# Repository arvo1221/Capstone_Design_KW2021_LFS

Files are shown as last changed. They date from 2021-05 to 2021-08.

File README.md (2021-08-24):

# Capstone_Design_KW2021\
...

Environment : 

OS :16.04 ubuntu ros-kinetic \
Library  : PCL (at least 1.7) \
         : Eigen 3 \
         : RBDL 

# HardWare description



# System Architecture
캡스톤system아키텍처

#Video
https://www.youtube.com/watch?v=N5EMGGjnUHE

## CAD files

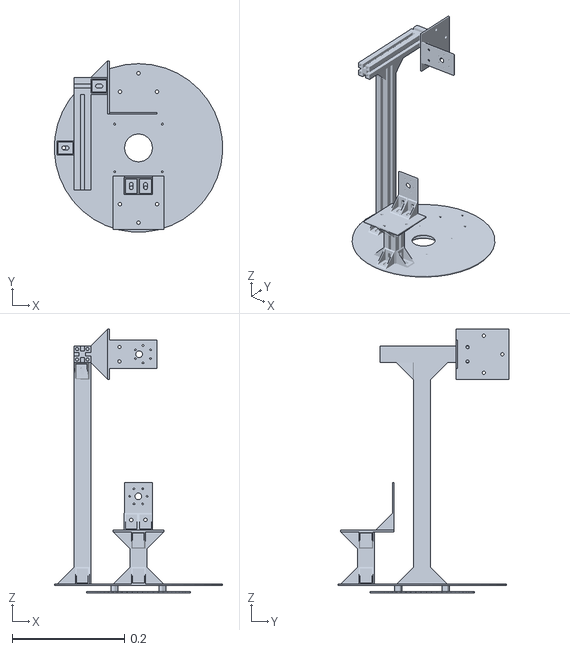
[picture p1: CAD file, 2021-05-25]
capstone_ws/src/turret_description/meshes/Yaw_link.STL
0.3 x 0.305 x 0.47

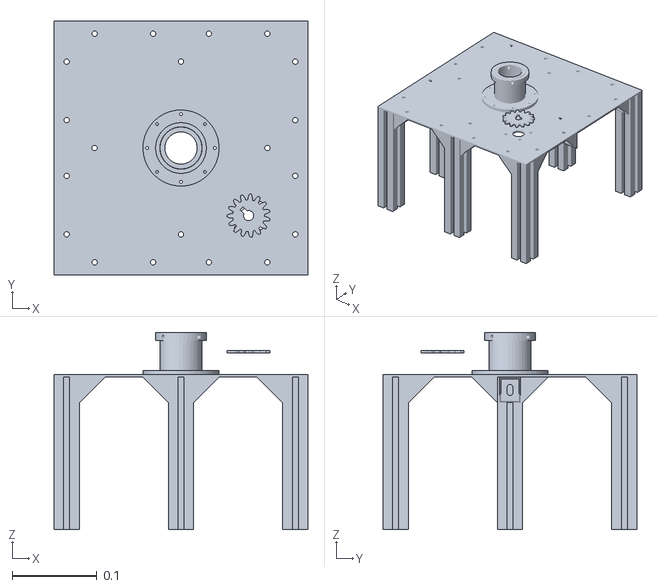
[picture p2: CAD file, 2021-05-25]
capstone_ws/src/turret_description/meshes/Base_link.STL
0.3 x 0.3 x 0.233

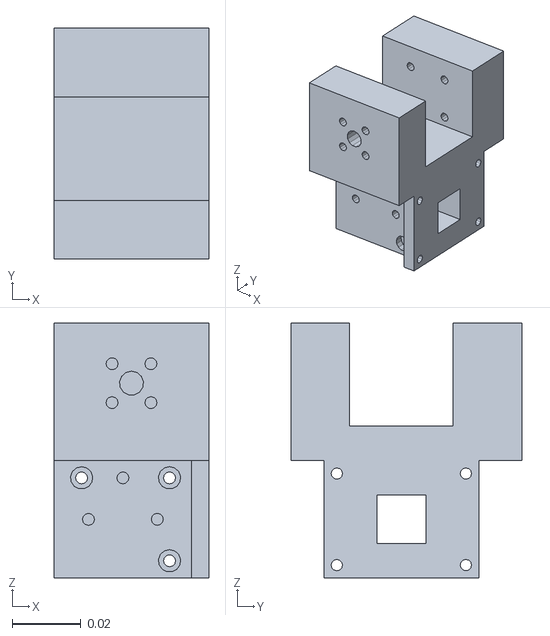
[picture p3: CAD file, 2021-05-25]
capstone_ws/src/turret_description/meshes/Pitch_link.STL
0.045 x 0.067 x 0.0741

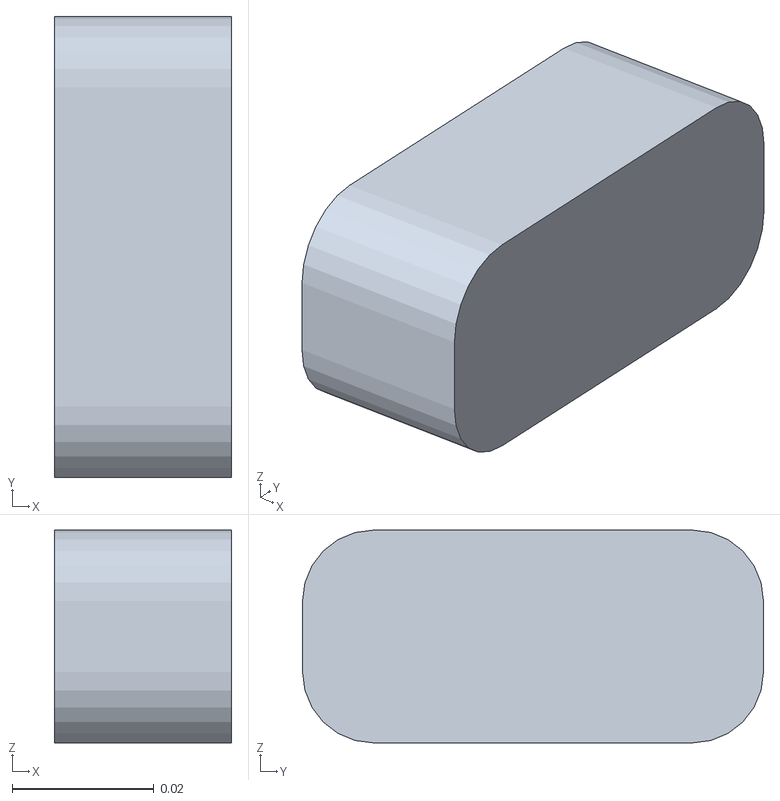
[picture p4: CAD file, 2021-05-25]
capstone_ws/src/turret_description/meshes/Camera_link.STL
0.025 x 0.065 x 0.03

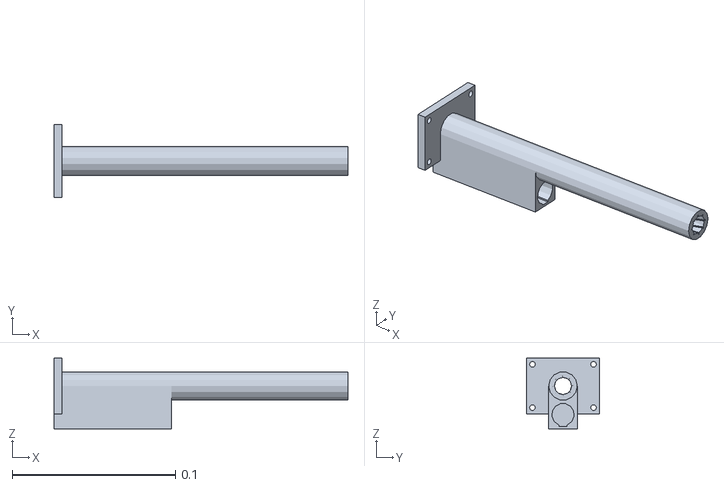
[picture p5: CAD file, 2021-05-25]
capstone_ws/src/turret_description/meshes/Rail_link.STL
0.18 x 0.045 x 0.0433

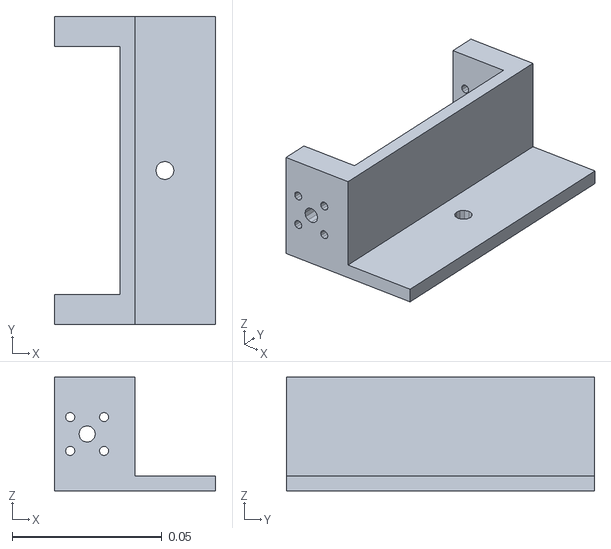
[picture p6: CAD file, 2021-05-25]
capstone_ws/src/turret_description/meshes/Camera_pitch_link.STL
0.054 x 0.103 x 0.038

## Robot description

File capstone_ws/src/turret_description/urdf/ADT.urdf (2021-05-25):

<?xml version="1.0" encoding="utf-8"?>
<!-- This URDF was automatically created by SolidWorks to URDF Exporter! Originally created by Stephen Brawner (brawner@gmail.com) 
     Commit Version: 1.6.0-1-g15f4949  Build Version: 1.6.7594.29634
     For more information, please see http://wiki.ros.org/sw_urdf_exporter -->
<robot name="ADT">
  <link name="Base_link">
    <inertial>
      <origin xyz="0.00064843481110697 -0.00978158089789138 0.122884766067913" rpy="0 0 0" />
      <mass value="1.19126257965004" />
      <inertia ixx="0.0182930869614911" ixy="-6.25115399086919E-05" ixz="6.53311402369967E-07" iyy="0.0182124664184306" iyz="-5.20847440153275E-06" izz="0.0274927596805442" />
    </inertial>
    <visual>
      <origin xyz="0 0 0" rpy="0 0 0" />
      <geometry>
        <mesh filename="package://ADT/meshes/Base_link.STL" />
      </geometry>
      <material name="">
        <color rgba="0.792156862745098 0.819607843137255 0.933333333333333 1" />
      </material>
    </visual>
    <collision>
      <origin xyz="0 0 0" rpy="0 0 0" />
      <geometry>
        <mesh filename="package://ADT/meshes/Base_link.STL" />
      </geometry>
    </collision>
  </link>
  <link name="Yaw_link">
    <inertial>
      <origin xyz="-0.0468029345624889 -0.0022094355333272 0.153762936135576" rpy="0 0 0" />
      <mass value="0.792271578967464" />
      <inertia ixx="0.0264772081268204" ixy="0.000711423814329615" ixz="0.0044932500059605" iyy="0.0261514783205725" iyz="-0.00334003583814821" izz="0.00686392856817581" />
    </inertial>
    <visual>
      <origin xyz="0 0 0" rpy="0 0 0" />
      <geometry>
        <mesh filename="package://ADT/meshes/Yaw_link.STL" />
      </geometry>
      <material name="">
        <color rgba="0.792156862745098 0.819607843137255 0.933333333333333 1" />
      </material>
    </visual>
    <collision>
      <origin xyz="0 0 0" rpy="0 0 0" />
      <geometry>
        <mesh filename="package://ADT/meshes/Yaw_link.STL" />
      </geometry>
    </collision>
  </link>
  <joint name="Yaw_link_joint" type="revolute">
    <origin xyz="0.00087547 -0.010086 0.2234" rpy="0 0 0.017045" />
    <parent link="Base_link" />
    <child link="Yaw_link" />
    <axis xyz="0 0 -1" />
    <limit lower="0" upper="0" effort="0" velocity="0" />
  </joint>
  <link name="Pitch_link">
    <inertial>
      <origin xyz="0.000868332385022257 0.00177256263735842 -0.0149035880305662" rpy="0 0 0" />
      <mass value="0.110851272025115" />
      <inertia ixx="8.44547728245917E-05" ixy="1.80829231564459E-07" ixz="2.90104125510869E-06" iyy="5.94659742301498E-05" iyz="-2.32896816206657E-06" izz="6.41123814690757E-05" />
    </inertial>
    <visual>
      <origin xyz="0 0 0" rpy="0 0 0" />
      <geometry>
        <mesh filename="package://ADT/meshes/Pitch_link.STL" />
      </geometry>
      <material name="">
        <color rgba="0.792156862745098 0.819607843137255 0.933333333333333 1" />
      </material>
    </visual>
    <collision>
      <origin xyz="0 0 0" rpy="0 0 0" />
      <geometry>
        <mesh filename="package://ADT/meshes/Pitch_link.STL" />
      </geometry>
    </collision>
  </link>
  <joint name="Pitch_link_joint" type="revolute">
    <origin xyz="-0.00030345 0 0.156" rpy="0 0 0" />
    <parent link="Yaw_link" />
    <child link="Pitch_link" />
    <axis xyz="0 1 0" />
    <limit lower="0" upper="0" effort="0" velocity="0" />
  </joint>
  <link name="Rail_link">
    <inertial>
      <origin xyz="0.0848289093290519 -5.00613901806557E-05 -0.0047495538421316" rpy="0 0 0" />
      <mass value="0.0461878510377165" />
      <inertia ixx="6.92222175379136E-06" ixy="1.80610649725021E-10" ixz="-6.0270127189008E-06" iyy="0.000133325014343347" iyz="-2.01173873432802E-10" izz="0.000131280254302823" />
    </inertial>
    <visual>
      <origin xyz="0 0 0" rpy="0 0 0" />
      <geometry>
        <mesh filename="package://ADT/meshes/Rail_link.STL" />
      </geometry>
      <material name="">
        <color rgba="0.792156862745098 0.819607843137255 0.933333333333333 1" />
      </material>
    </visual>
    <collision>
      <origin xyz="0 0 0" rpy="0 0 0" />
      <geometry>
        <mesh filename="package://ADT/meshes/Rail_link.STL" />
      </geometry>
    </collision>
  </link>
  <joint name="Rail_link_joint" type="fixed">
    <origin xyz="0 0 -0.0395" rpy="0 0 0" />
    <parent link="Pitch_link" />
    <child link="Rail_link" />
    <axis xyz="0 0 0" />
  </joint>
  <link name="Camera_pitch_link">
    <inertial>
      <origin xyz="0.0137176751406853 -0.00447291778436898 -0.00464355582105691" rpy="0 0 0" />
      <mass value="0.0488857805315246" />
      <inertia ixx="7.04275934438531E-05" ixy="-5.36553236462091E-08" ixz="3.59137069936737E-06" iyy="1.49745449406692E-05" iyz="1.81628073187509E-08" izz="7.12701375699277E-05" />
    </inertial>
    <visual>
      <origin xyz="0 0 0" rpy="0 0 0" />
      <geometry>
        <mesh filename="package://ADT/meshes/Camera_pitch_link.STL" />
      </geometry>
      <material name="">
        <color rgba="0.792156862745098 0.819607843137255 0.933333333333333 1" />
      </material>
    </visual>
    <collision>
      <origin xyz="0 0 0" rpy="0 0 0" />
      <geometry>
        <mesh filename="package://ADT/meshes/Camera_pitch_link.STL" />
      </geometry>
    </collision>
  </link>
  <joint name="Camera_pitch_link_joint" type="revolute">
    <origin xyz="0.001 0 0.4091" rpy="0 0 0" />
    <parent link="Yaw_link" />
    <child link="Camera_pitch_link" />
    <axis xyz="0 -1 0" />
    <limit lower="0" upper="0" effort="0" velocity="0" />
  </joint>
  <link name="Camera_link">
    <inertial>
      <origin xyz="-0.0124847400809419 3.38190441206976E-08 6.09664012027888E-05" rpy="0 0 0" />
      <mass value="0.0463212382951515" />
      <inertia ixx="1.84581667049109E-05" ixy="-1.05879118406788E-21" ixz="7.11172987522141E-09" iyy="5.69302257282933E-06" iyz="1.33849762299999E-20" izz="1.7614897342325E-05" />
    </inertial>
    <visual>
      <origin xyz="0 0 0" rpy="0 0 0" />
      <geometry>
        <mesh filename="package://ADT/meshes/Camera_link.STL" />
      </geometry>
      <material name="">
        <color rgba="0.792156862745098 0.819607843137255 0.933333333333333 1" />
      </material>
    </visual>
    <collision>
      <origin xyz="0 0 0" rpy="0 0 0" />
      <geometry>
        <mesh filename="package://ADT/meshes/Camera_link.STL" />
      </geometry>
    </collision>
  </link>
  <joint name="Camera_link_joint" type="fixed">
    <origin xyz="0.041 -0.0043929 0.0010012" rpy="0 -2.6267E-05 0" />
    <parent link="Camera_pitch_link" />
    <child link="Camera_link" />
    <axis xyz="0 0 0" />
  </joint>
</robot>

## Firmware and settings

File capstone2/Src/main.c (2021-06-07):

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

/* Includes ------------------------------------------------------------------*/
#include "main.h"

/* USER CODE BEGIN Includes */
#include "string.h"
#include "math.h"
#include "dataType.h"

/* USER CODE END Includes */

ADC_HandleTypeDef hadc1;
DMA_HandleTypeDef hdma_adc1;

TIM_HandleTypeDef htim2;
TIM_HandleTypeDef htim3;
TIM_HandleTypeDef htim4;
TIM_HandleTypeDef htim11;

UART_HandleTypeDef huart6;
DMA_HandleTypeDef hdma_usart6_rx;

/* USER CODE BEGIN PV */
#define RX_BUFFER_SIZE 256
#define TX_BUFFER_SIZE 256
#define dt1 0.0005
#define dt2 0.005
#define dt3 0.05
#define ppr 4000
#define pi 3.141592653589793
#define get_dma_data_length() huart6.hdmarx->Instance->NDTR
#define get_dma_total_size() huart6.RxXferSize
#define shooting 6000
#define noshooting 3500

int32_t encoder_cnt_R = 0;
int32_t encoder_cnt_pre_R = 0;
int32_t cnt_R = 0;
int32_t k = 0;
int16_t mode = 0;
volatile double angular_velocity_R = 0;
volatile double angular_velocity_pre_R = 0;
volatile double theta = 0;
volatile uint16_t Motor_CCR_R = 0;
volatile uint16_t shoot_degree = 0;
volatile uint32_t timer = 0;
volatile uint32_t shoot_timer = 0;

volatile double Kpc = 0.9;//45.5672;
volatile double Kic = 720;//8685.17;

volatile double Kac = 0;
volatile double Kps = 0.7;//0.7
volatile double Kis = 5;//5

volatile double Kas = 0;
volatile double Es = 0;
volatile double Eis = 0;
volatile double V_control = 0;//speed
volatile double rep_r = 0;
volatile double rep_current = 0;
volatile double Ecurrent = 0;
volatile double EScurrent = 0;
volatile double C_control = 0;
volatile double Motor_PWM = 0;
volatile double current_saturation = 1.5;

volatile double Kpp = 6.5;//8.0
volatile double Kip = 0;
volatile double Kdp = 0.23;//0.248
volatile double Kap = 0;
volatile double Eposition = 0;
volatile double ESposition = 0;
volatile double Edposition = 0;
volatile double rep_position = 0;
volatile double rep_degree = 0;
volatile double P_control;
volatile double velocity_saturation = 2.5;

volatile uint32_t adcVal[2];
volatile uint32_t adcVal_pre;
volatile double current_offset = 3121.5;
volatile double current;
volatile double current_pre;
volatile double current_mv[10];
uint16_t c_cnt = 0;
volatile double tau = 0.00051;
volatile double current_sum = 0;

int16_t watch_current;
int16_t watch_repc;
int16_t watch_velocity;
int16_t watch_repv;
int16_t watch_repp;
int16_t watch_degree;

uint8_t rx_dma_buffer[RX_BUFFER_SIZE];
uint8_t rx_buffer[RX_BUFFER_SIZE];
uint32_t rx_size = 0;
uint8_t tx_buffer[TX_BUFFER_SIZE];
uint8_t tx_len;
volatile unsigned char g_tail_pos = 255;
volatile unsigned char g_head_pos;
volatile Packet_t g_PacketBuffer;
volatile unsigned char g_PacketMode;
volatile unsigned char g_ID=1;
volatile unsigned char checkSize;
volatile unsigned char g_checksum;
volatile Packet_t g_Tx_Packet;
volatile unsigned char g_Tx_checksum;
volatile int g_SendFlag;


volatile uint16_t shoot = 0;
/* USER CODE END PV */

void SystemClock_Config(void);
static void MX_GPIO_Init(void);
static void MX_DMA_Init(void);
static void MX_TIM4_Init(void);
static void MX_TIM3_Init(void);
static void MX_TIM2_Init(void);
static void MX_USART6_UART_Init(void);
static void MX_ADC1_Init(void);
static void MX_TIM11_Init(void);
/* USER CODE BEGIN PFP */

/* USER CODE END PFP */

/* USER CODE BEGIN 0 */

void Uart_rx_dma_handler() {
  uint8_t cnt;
  uint8_t i;

  rx_size = 0;
  g_head_pos = huart6.RxXferSize - huart6.hdmarx->Instance->NDTR -1;
  
  while(g_tail_pos != g_head_pos) {
    switch (g_PacketMode) {
      case 0:
        if (rx_dma_buffer[g_tail_pos] == 0xFE) {//Header check
          checkSize++;
          if (checkSize == 4) g_PacketMode = 1;// header 4개가 다 들어왔으면 1번 모드로 변경
        }
        else checkSize = 0;	//초기화
      break;
      case 1:
        g_PacketBuffer.buffer[checkSize++] = rx_dma_buffer[g_tail_pos]; //checkSize 8될때 까지 g_PacketBuffer.buffer에 받아온 값 담기(size,mode,g_checksum)
        if (checkSize == 8) g_PacketMode = 2;
      break;
     
      case 2:
       g_PacketBuffer.buffer[checkSize++] = rx_dma_buffer[g_tail_pos];
       g_checksum += rx_dma_buffer[g_tail_pos];
       
       if (checkSize == g_PacketBuffer.data.size){					//data size만큼 버퍼읽음
         if (g_checksum == g_PacketBuffer.data.check){					// checksum check
            switch(g_PacketBuffer.data.mode){				// 모든게 올바르면, Get target position, Velocity limit Current Limit
               case 2:
                 rep_degree = -g_PacketBuffer.data.pos_P/1000.;
                 velocity_saturation = g_PacketBuffer.data.vel_P/1000.;
                 shoot = g_PacketBuffer.data.shoot;
               break;
            }
         }
         //초기화
         g_checksum = 0;						
         g_PacketMode = 0;
         checkSize = 0;              
       }
       else if(checkSize > g_PacketBuffer.data.size || checkSize > sizeof(Packet_t)){		//오류시 초기화
           g_checksum = 0;
           g_PacketMode = 0;
           checkSize = 0;
       }
    }
    
     if(g_SendFlag >9) {			
        g_SendFlag = 0;
        g_Tx_Packet.data.header[0] = g_Tx_Packet.data.header[1] = g_Tx_Packet.data.header[2] = g_Tx_Packet.data.header[3] = 0xFE;
        g_Tx_Packet.data.id = g_ID;							//motor id 다만 이번과제에선 사용하지 않음
        g_Tx_Packet.data.size = sizeof(Packet_data_t);
        g_Tx_Packet.data.mode = 3;						//mode 3
        g_Tx_Packet.data.check = 0;
        
        g_Tx_Packet.data.pos_P = -theta*180/pi*1000;
        g_Tx_Packet.data.vel_P = -angular_velocity_R* 1000;
        g_Tx_Packet.data.shoot = shoot;
        
        for(int i = 8; i< sizeof(Packet_t);i++)		// checksum 제작
        g_Tx_Packet.data.check += g_Tx_Packet.buffer[i];
        
        for(int i =0; i<g_Tx_Packet.data.size;i++){		//송신
          tx_buffer[i] = g_Tx_Packet.buffer[i];
        }
        HAL_UART_Transmit(&huart6, tx_buffer, g_Tx_Packet.data.size,10);
    }
    g_tail_pos++;
  }        
        
}

void HAL_TIM_PeriodElapsedCallback(TIM_HandleTypeDef *htim) {
  if(htim == &htim4) {
    timer++;
    //HAL_GPIO_WritePin(GPIOA,GPIO_PIN_4,GPIO_PIN_SET);

    HAL_ADC_Start_DMA(&hadc1,(uint32_t*)adcVal,1);
    adcVal[0] = (double)(0.00005*adcVal[0] + tau*adcVal_pre)/(tau+0.00005);
    adcVal_pre = adcVal[0];
    current_sum -= current_mv[c_cnt];
    current_mv[c_cnt] = adcVal[0];
    current_sum += current_mv[c_cnt];
    c_cnt = (c_cnt+1)%10;
    current = (double)(current_sum/10.-current_offset)/4096*33.;
    if(mode == 1) {
      k++;
      if(k > 8000) {
        current_offset = current_sum/10.;
        Ecurrent = 0;
        EScurrent = 0;
        Es = 0;
        Eis = 0;
        Motor_CCR_R = 0;
        timer = 1;   
        C_control = 0;
        mode = 2;
      }
    }
    else if(mode ==2) {
      if(timer%1000 == 0) {
        
        rep_position = (double)rep_degree*pi/180;//input degree output radian
        /*
        if(theta < -1 * pi) { 
          theta += 2.0*pi;
        }
        else if(theta > pi) {
          theta -= 2.0*pi;
        }
        if(rep_position < -1 * pi) { 
          rep_position += 2.0*pi;
        }
        else if(rep_position > pi) {
          rep_position -= 2.0*pi;
        }*/
        Edposition = Eposition;
        Eposition = (double)rep_position - theta;
        //ESposition += (double)Eposition;
        //Kap = 1./(3*Kpp);
        P_control = (double)(Kpp * Eposition +/*Kip*ESposition*dt3 +*/ Kdp *(Eposition - Edposition)/dt3);
        
        if(P_control >= velocity_saturation) {
          //ESposition -= (double)(P_control - velocity_saturation)*Kap;
          P_control = velocity_saturation;
        }
        else if(P_control <= -velocity_saturation) {
          //ESposition -= (double)(P_control + velocity_saturation)*Kap;
          P_control = -velocity_saturation;
        }
        if(shoot == 1) {
          shoot_timer++;
          shoot_degree =  shooting;
          if(shoot_timer == 10) {
            shoot_degree = noshooting;
            shoot = 0;
            shoot_timer = 0;
            }
        }
        else if(shoot == 0) {
            shoot_degree = noshooting;
        }
      
        g_SendFlag++;
        timer = 0;
      }
      
      if(timer%100 == 0) {
        encoder_cnt_pre_R = encoder_cnt_R;
        encoder_cnt_R = TIM3->CNT;
        cnt_R = encoder_cnt_R - encoder_cnt_pre_R;
        rep_r = P_control;
        
        if(encoder_cnt_R < 500 && encoder_cnt_pre_R > 64500 ) cnt_R += 65535;
        else if(encoder_cnt_pre_R < 500 && encoder_cnt_R > 64500) cnt_R -= 65535;
        
        theta += (double)(2*pi*cnt_R/ppr);
        angular_velocity_R = (double)(2*pi*cnt_R/ppr)/dt2;
        
        Es = (double)(rep_r - angular_velocity_R);
        Eis += (double)Es;
        
        V_control = (double)(Kps * Es + Kis * Eis*dt2);
          
        if(V_control >= current_saturation) {
          Eis -= (double)(V_control - current_saturation)*Kas;
          V_control = current_saturation;
        }
        else if(V_control <= -current_saturation) {
          Eis -= (double)(V_control + current_saturation)*Kas;
          V_control = -current_saturation;
        }
        
      }
      
      if(timer%10 == 0) {
        //current[0] = (double)(0.005*current_n[0] + tau*current_pre[0])/(tau+0.005);
        //current_pre[0] = current[0];
        rep_current = V_control;
        Ecurrent = (double)(rep_current-current);
        C_control = (double)(Kpc * Ecurrent + Kic * EScurrent * dt1);
        //C_control += 0.005*angular_velocity_R;
        EScurrent += (double)Ecurrent;
        
        if(C_control >= 12) {
          EScurrent -= (C_control - 12)*Kac;
          C_control = 12;
        }
        else if(C_control <= -12) {
          EScurrent -= (C_control + 12)*Kac;
          C_control = -12;
        }
        
        if(C_control < 0 ) {
          HAL_GPIO_WritePin(GPIOA,GPIO_PIN_5,GPIO_PIN_SET);
          C_control = -C_control;
        }
        else {
         HAL_GPIO_WritePin(GPIOA,GPIO_PIN_5,GPIO_PIN_RESET);
        }
      }
      
      Motor_PWM = (double)C_control*374.9166666667;
      Motor_CCR_R = (uint16_t)Motor_PWM;
      //HAL_GPIO_WritePin(GPIOA,GPIO_PIN_4,GPIO_PIN_RESET);
    }
    TIM4->CCR1 = Motor_CCR_R;
    TIM11->CCR1 = shoot_degree;
    /*
    servomotor 20ms prescale 60 count 60000
    */
    watch_current = 1000*current;
    watch_repc = 1000*rep_current ;
    watch_velocity = 1000*angular_velocity_R;
    watch_repv = 1000 * rep_r;
    watch_repp = 1000 *rep_degree;
    watch_degree = 1000 *theta/pi*180.;
  }
}

/* USER CODE END 0 */

/**
  * @brief  The application entry point.
  * @retval int
  */
int main(void)
{
  /* USER CODE BEGIN 1 */
      Motor_CCR_R = 0;
      mode=1;
  /* USER CODE END 1 */
  

  /* MCU Configuration--------------------------------------------------------*/

  /* Reset of all peripherals, Initializes the Flash interface and the Systick. */
  HAL_Init();

  /* Configure the system clock */
  SystemClock_Config();

  /* Initialize all configured peripherals */
  MX_GPIO_Init();
  MX_DMA_Init();
  MX_TIM4_Init();
  MX_TIM3_Init();
  MX_TIM2_Init();
  MX_USART6_UART_Init();
  MX_ADC1_Init();
  MX_TIM11_Init();
  /* USER CODE BEGIN 2 */
  HAL_TIM_Encoder_Start(&htim3,TIM_CHANNEL_ALL);
  Kac = 1./(2.1*Kpc);
  Kas = 1./(1.1*Kps);
  Kap = 1./(3*Kpp);
  HAL_UART_Receive_DMA(&huart6, rx_dma_buffer, RX_BUFFER_SIZE);
  HAL_TIM_PWM_Start(&htim4, TIM_CHANNEL_1);
  HAL_TIMEx_PWMN_Start(&htim4, TIM_CHANNEL_1);
  HAL_TIM_PWM_Start(&htim11, TIM_CHANNEL_1);
  HAL_TIMEx_PWMN_Start(&htim11, TIM_CHANNEL_1);//3000 1ms
  //HAL_TIM_PWM_Start(&htim4, TIM_CHANNEL_2);
  //HAL_TIMEx_PWMN_Start(&htim4, TIM_CHANNEL_2);
  //HAL_TIM_Encoder_Start(&htim2,TIM_CHANNEL_ALL);
  //HAL_TIM_Encoder_Start(&htim3,TIM_CHANNEL_ALL);
  //HAL_GPIO_WritePin(GPIOA,GPIO_PIN_4,GPIO_PIN_SET);
  HAL_GPIO_WritePin(GPIOA,GPIO_PIN_5,GPIO_PIN_SET);//Set CCW //RESET CW
  HAL_TIM_Base_Start_IT(&htim4);
  
  /* USER CODE END 2 */

  /* Infinite loop */
  /* USER CODE BEGIN WHILE */
  while (1)
  {

    /* USER CODE END WHILE */

    /* USER CODE BEGIN 3 */
  Uart_rx_dma_handler();
  }
  /* USER CODE END 3 */
}

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


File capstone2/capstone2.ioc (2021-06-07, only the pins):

Mcu.UserName=STM32F446RETx
PA0-WKUP.Signal=S_TIM2_CH1_ETR
PA1.Signal=S_TIM2_CH2
PA4.Signal=GPIO_Output
PA5.Signal=GPIO_Output
PA6.Signal=S_TIM3_CH1
PA7.Signal=S_TIM3_CH2
PB6.Signal=S_TIM4_CH1
PB7.Signal=S_TIM4_CH2
PB9.Signal=S_TIM11_CH1
PC14-OSC32_IN.Signal=RCC_OSC32_IN
PC15-OSC32_OUT.Signal=RCC_OSC32_OUT
PC2.Signal=ADCx_IN12
PC6.Signal=USART6_TX
PC7.Signal=USART6_RX
PH0-OSC_IN.Signal=RCC_OSC_IN
PH1-OSC_OUT.Signal=RCC_OSC_OUT

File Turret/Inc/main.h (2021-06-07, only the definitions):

#define B1_Pin GPIO_PIN_13
#define B1_GPIO_Port GPIOC
#define LD2_Pin GPIO_PIN_5
#define LD2_GPIO_Port GPIOA
#define TMS_Pin GPIO_PIN_13
#define TMS_GPIO_Port GPIOA
#define TCK_Pin GPIO_PIN_14
#define TCK_GPIO_Port GPIOA
#define SWO_Pin GPIO_PIN_3
#define SWO_GPIO_Port GPIOB

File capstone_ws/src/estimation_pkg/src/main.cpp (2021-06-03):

#include "../include/estimation_pkg/turret_controller.hpp"
#include "../include/estimation_pkg/Kinematics.h"

int main(int argc, char **argv)
{
    ros::init(argc, argv, "main");
    ros::NodeHandle nh("~");

    // std::string yaml_path;
    // nh.getParam("yaml_path", yaml_path);

    // YAMLConfig config;
    // config.loadConfig(yaml_path);
    std::string port;
    std::string port2;
    int baudrate;

    
    nh.getParam("port",port);
    nh.getParam("port2",port2);
    nh.getParam("baudrate",baudrate);

    turret_controller_interface CommandCenter(nh, 10);
    //std::string port = "/dev/ttyUSB0";
   // std::string port2 = "/dev/ttyUSB1";

    CommandCenter.OpenTurretSerial(port,115200);
    CommandCenter.OpenCameraSerial(port2,115200);

    while(ros::ok()){
        ros::spinOnce();
    }

    CommandCenter.killProcess();
    return 0;
}

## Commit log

2021-05-16 Camera Pan Tilt Controller & Servomotor Pan Tilt Motor current,velocity,position controller (finished) servomotor(shoot target) ..ing Packet receive transmit..ing
2021-05-16 Add Servomotor Settiing 20ms -> prescale 60,count 60000
2021-05-18 turret controller, turret desciptor and turret_assembly
    [Camera_Link.STL, Camera_Pitch_Link.STL, Pitch_Link.STL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]
2021-05-24 Create CAD
2021-05-24 kinematic solver update
2021-05-25 kinematics Chain update
    [ADT.csv, ADT.urdf, Base_link.STL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]
2021-05-26 update Yaw and Pitch Target Algorithm
2021-05-27 filter X
2021-05-29 Board2 Packet test Packet_t pos_P(degree) , vel_P(rad/s) , shooting state "successful"
2021-05-29 servo motor success servo tim9 -> tim11 20ms, prescale 60 count 60000 1ms 3000 2ms 6000 pushing time 500ms
2021-06-03 6/3 senser and transform calibration done
2021-06-07 STcodeUpdate
    Turret, camera, servo code update
2021-06-07 Servo change
    servo init change
2021-07-28 System Architecture upload
    그전 사진 잘 못 업로드함

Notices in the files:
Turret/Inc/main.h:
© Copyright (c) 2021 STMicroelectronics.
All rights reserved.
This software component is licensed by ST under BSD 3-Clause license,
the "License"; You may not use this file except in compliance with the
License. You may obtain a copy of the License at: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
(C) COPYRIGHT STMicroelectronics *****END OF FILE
